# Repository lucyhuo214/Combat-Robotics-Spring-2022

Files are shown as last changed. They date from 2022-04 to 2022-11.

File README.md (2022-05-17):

# Combat-Robotics-Spring-2022
This repository includes the files for the Combat Robotics independent study at Duke University under the mentorship of Dr. Tyler Bletsch. Contributors to this project are Lucy Huo, Richard Kim, and Emily Shao.

## Project Overview
The task for this project was to build a combat robot according to the SPARC Robot Construction Specifications in the antweight class. The final project was a combat robot with a holonomic drive system. The robot uses omni wheels and an inertial measurement unit (IMU) sensor to achieve this task, correcting errors in misalignment based on IMU sensor feedback without the use of encoders on the wheels.

The primary components of the combat robot design are the three-omni-wheel kiwi drive system and the implementation of a BNO055 accelerometer to enable closed loop control, stabilizing the drive system. The software control for the robot is implemented using an Arduino Nano microcontroller.

## Holonomic Drive System
The final combat robot moves using a holonomic drive system. Holonomic drive is a drive system in which the robot’s degrees of freedom of movement are equal to the robot’s degrees of control. The combat robot in this project can move freely in the X- and Y-directions without turning, successfully implementing a holonomic drive system.

The robot uses a kiwi drive system to accomplish this, which is a form of holonomic drive that uses three omni wheels placed 120 degrees apart. Omni wheels have small rollers that are perpendicular to the direction of rotation for a wheel, allowing the wheel to roll sideways along with going forward and backwards. Omni wheels are also able to move laterally,  giving the robot full range of motion in any direction.

The CombatRoboticsHolonomic.ino script includes the robot's implementation of a holonomic drive system using kiwi drive.

## PID Closed Loop Control System
The greatest challenge that arose while implementing kiwi drive was that the robot would veer off in undesired directions due to various internal or external factors. These might include slight variations in motor performance or uneven friction within the combat arena. In most kiwi drive systems, encoders are placed on each of the three wheels to correct misalignment. However, this robot used feedback from an IMU sensor to detect and correct these misalignments without the use of any encoders.

The self-correcting control is implemented using the BNO055 accelerometer sensor. The accelerometer is mounted to the base of the robot chassis, allowing it to remain fixed to the robot and accurately gather orientation data while the robot is in motion.

The self-oriented control system is implemented using a form of closed loop control, in which portions of the output signal are used as input to the system to reduce errors or achieve system stability. For this project, the output was the yaw value from the BNO055, which was then used as an input to the kiwi drive calculations to ensure a more stable holonomic drive system.

The robot utilizes PID control, also known as Proportional, Integral, and Derivative control, to achieve this function. The proportional control adjusts the output in proportion to the error measured. The derivative control limits the overshoot of the proportional adjustment, helping the robot converge on its goal orientation faster. Finally, the integral is normally used to reduce static error in a system, but was not implemented in this project because it was negligible while in combat.

The CombatRoboticsSelfOrienting.ino script is a proof-of-concept demonstrating the ability of the robot to use PID closed loop control. The script enables the robot to always face a set absolute orientation, self correcting towards this setpoint using applications of PID control theory.

Finally, the CombatRoboticsFinalCode.ino script includes the final iteration of software control for the combat robot. It moderates the robot's holonomic drive system using PID control, while still allowing the robot driver to move and rotate in all directions in the XY-plane as desired.

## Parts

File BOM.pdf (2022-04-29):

BOM
ID
| BOM | QUANTITY
1 | 300 RPM with Metal Gearbox (N-20) | 3
2 | 2212 2200kv Brushless Motor | 1
3 | Brushed Motor ESC | 2 (or 1 if there are 3 outputs)
4 | BNO055 | 1
5 | ElectroCookie Mini Board | 1
6 | 3 pin 12V switch | 1
7 | Jst syp connector (Male + Female) | 5
8 | XT60 Connector (Male + Female) | 2
9 | Mc6c 2.4g 6ch Controller | 1

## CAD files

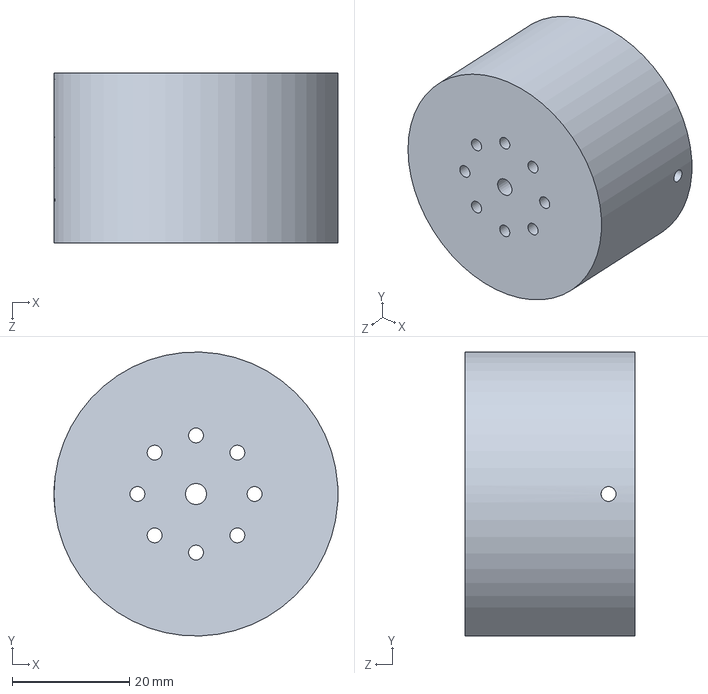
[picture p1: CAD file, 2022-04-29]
CAD Files/brushless motor insert v2.SLDPRT
48.5 x 48.5 x 29.0 mm

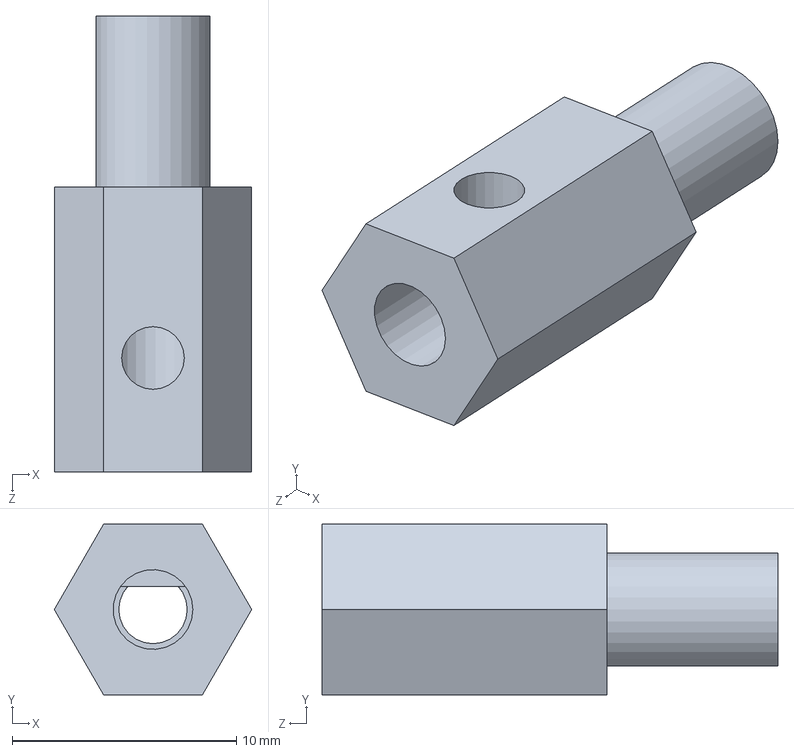
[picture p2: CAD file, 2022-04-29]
CAD Files/hex wheel insert.SLDPRT
8.80 x 7.62 x 20.3 mm

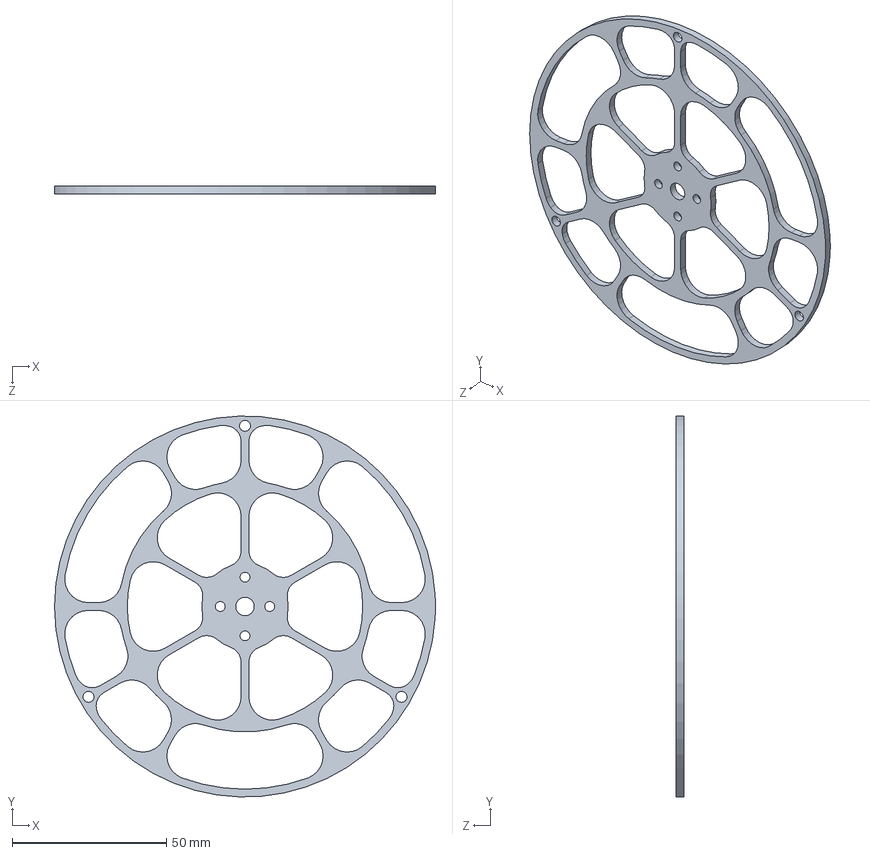
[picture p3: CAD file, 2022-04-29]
CAD Files/cover.SLDPRT
123.4 x 123.4 x 2.54 mm

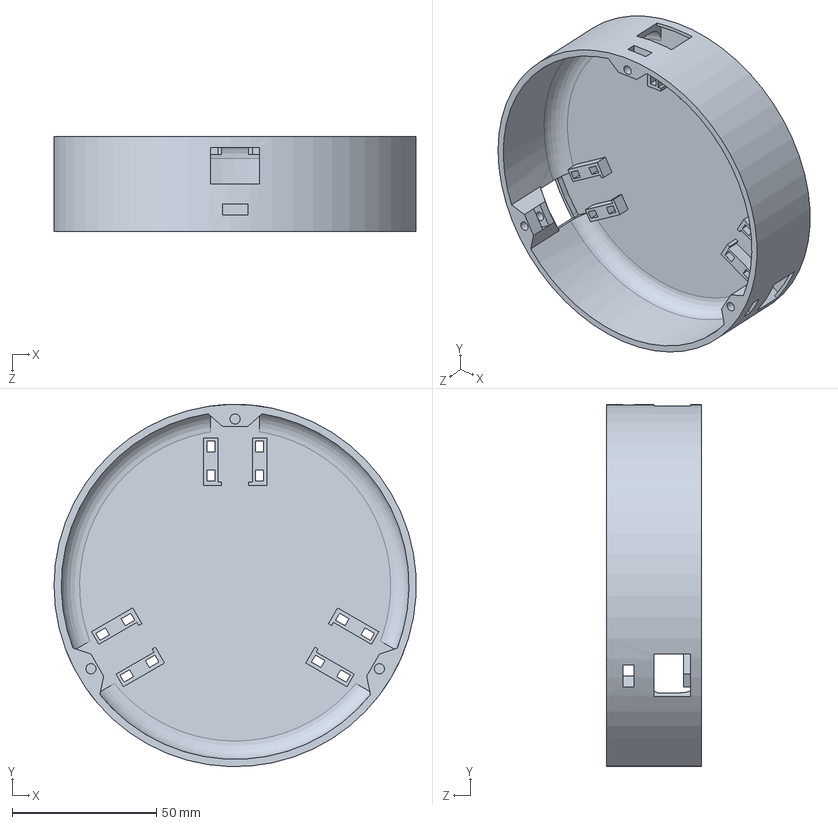
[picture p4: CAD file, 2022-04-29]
CAD Files/robot chassis.SLDPRT
125.6 x 125.7 x 33.0 mm

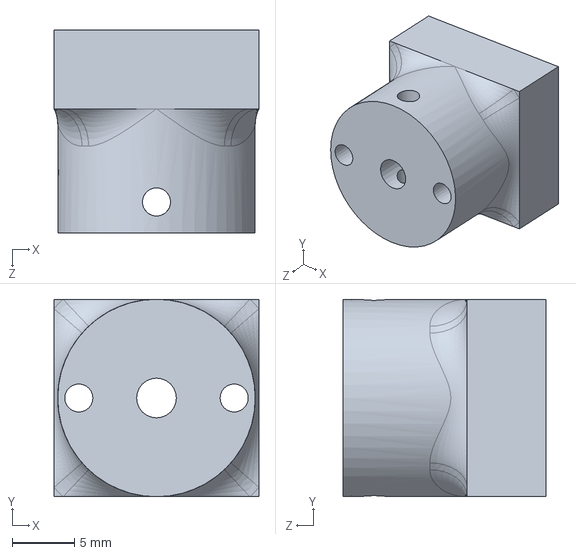
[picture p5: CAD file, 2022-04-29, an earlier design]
CAD Files/brushless motor insert v1.SLDPRT
16.5 x 15.9 x 16.4 mm

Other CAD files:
STL files/brushless motor insert v1.STL
STL files/brushless motor insert v2.STL
STL files/cover.STL
STL files/hex wheel insert.STL
STL files/robot chassis.STL

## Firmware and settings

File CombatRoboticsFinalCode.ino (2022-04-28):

/* This Arduino script includes the final integrated code for the combat robot. 
It enables a kiwi function drive system that is moderated by closed loop PID control using a BNO055 accelerometer. */

//Libraries
#include <Wire.h>
#include <Servo.h>
#include <Adafruit_Sensor.h>
#include <Adafruit_BNO055.h>
#include <utility/imumaths.h> 

//Initialize BNO sensor
#define I2C_SDA A4
#define I2C_SCL A5

Adafruit_BNO055 bno = Adafruit_BNO055(55);

//Initialize servos
Servo wheelOne;
Servo wheelTwo;
Servo wheelThree;
int thetaPin = 7;
int forwardPin = 8;
int sidePin = 9;

//Initialize kiwi drive variables
int ser1;
int ser2;
int ser3; 

//Initialize x-orientation variables
float yaw;  //Absolute x-orientation value from BNO
int error;  //Error relative to setpoint
float setpoint = 180; //Absolute orientation goal of robot

//Initialize derivative time values
float error_before;
long time_before = micros();
int error_derivative; 

//Initialize PID control constants
float p_constant = 1.5;
float d_constant = 3;

void setup() {
  Serial.begin(9600);
  Wire.begin(I2C_SDA);
  Wire.begin(I2C_SCL);
  Serial.println("Orientation Sensor Test"); Serial.println("");

  /* Initialise the sensor */
  if(!bno.begin())
  {
    /* There was a problem detecting the BNO055 ... check your connections */
    Serial.print("Ooops, no BNO055 detected ... Check your wiring or I2C ADDR!");
    while(1);
  }
  delay(1000);
  bno.setExtCrystalUse(true);

//Initialize wheels
  wheelOne.attach(2);
  wheelTwo.attach(3);
  wheelThree.attach(4);
  calib();
  delay(5000);

//Initialize remote signals
  pinMode(forwardPin, INPUT); 
  pinMode(sidePin, INPUT);
  pinMode(thetaPin, INPUT);

  Serial.println("Done with setup");
}

void loop() {
  long thetaDuration = pulseIn(thetaPin, HIGH);  //Read PWM for theta input
  float thetaVal = map((float)thetaDuration, 1750.0, 950.0, -0.5, 0.5);
   
  long fwdDuration = pulseIn(forwardPin, HIGH);  //Read PWM for fwd input
  float fwdVal = map((float)fwdDuration, 1000.0, 1980.0, -1.0, 1.0);

  long sideDuration = pulseIn(sidePin, HIGH);  //Read PWM for side input
  float sideVal = map((float)sideDuration, 2030.0, 1080.0, -1.0, 1.0);

  if(thetaDuration<1350 || thetaDuration>1550){   //If driver is manually changing theta input
    delay(100);
    sensorEvent();
    setpoint = yaw;   //Adjusts robot setpoint
  }

  //Implements goal-seeking  
  sensorEvent();  //Reads x-orientation from BNO
  adjust();   //Corrects robot orientation with proportional adjustment
  updateDer();    //Updates error_derivative value
  
  kiwiFunct(fwdVal, sideVal, thetaVal);   //Calculate servo values with kiwi drive math


  ser1+=error;  //Corrects servo values proportionally
  ser2+=error;
  ser3+=error;

  ser1+=error_derivative;   //Dampens adjustment of servo values
  ser2+=error_derivative;
  ser3+=error_derivative;
  
  wheelOne.writeMicroseconds(ser1);   //Write values to drive servos
  wheelTwo.writeMicroseconds(ser2);
  wheelThree.writeMicroseconds(ser3);
  delay(10);
}

//Cacluates error relative to robot setpoint
void calcError(){ 
  if(setpoint<=180){ //Calculates error for setpoint less than 180 degrees
    if (yaw>setpoint && yaw<setpoint+180) 
      error = rotateLeft(yaw-setpoint);
    else if(yaw>0 && yaw<setpoint)
      error = rotateRight(setpoint-yaw);
    else if(yaw>setpoint+180 && yaw<360)
      error = rotateRight(360-yaw+setpoint);
  }
  else if(setpoint>180){ //Calculates error for setpoint greater than 180 degrees
    if (yaw>setpoint-180 && yaw<setpoint) 
      error = rotateRight(setpoint-yaw);
    else if(yaw>setpoint && yaw<360)
      error = rotateLeft(yaw-setpoint);
    else if(yaw>0 && yaw<setpoint-180)
      error = rotateLeft(360-setpoint+yaw);
  }
}


//Reorients robot to face forward while driving
void adjust(){
  if(yaw!=setpoint){
    calcError();
  }
}

//Calculates derivative value in PID to dampen adjustment
void updateDer(){
  float error_now = error;   //Records current robot orientation error
  float error_delta = error_now - error_before;  //Calculates change in error

  long time_now = micros();
  long time_delta = time_now - time_before;   //Calculates change in time

  error_derivative = (int)(d_constant * error_delta / (time_delta / 100000.0));  //Calculates error derivative
  
  error_before = error_now;   //Updates current error value
  time_before = time_now;   //Updates current time value
  }

//Rotation functions with goal-seeking
int rotateRight(float angle){
  float offset = angle;
  return (int)(-1 * p_constant * offset);   //Return scaled value for rightward adjustment
}

int rotateLeft(float angle){
  float offset = angle;
  return (int)(p_constant * offset);  //Return scaled value for leftward adjustment
}

//Stops robot
void calib(){
  wheelOne.writeMicroseconds(1500);
  wheelTwo.writeMicroseconds(1500);
  wheelThree.writeMicroseconds(1500);
}

//Prints servo values
void printSer(){
  Serial.print("Ser1: " );
  Serial.print(ser1);
  Serial.print("\tSer2: " );
  Serial.print(ser2);
  Serial.print("\tSer3: " );
  Serial.println(ser3);
}

//Calculates servo values
void kiwiFunct(float fwdVal, float sideVal, float thetaVal){
  float m1 = .5 * sideVal -sqrt(3)/2 * fwdVal + thetaVal;
  float m2 = .5 * sideVal + sqrt(3)/2 * fwdVal + thetaVal;
  float m3 = -1 * sideVal + thetaVal;

  float avg1 = (m1)/3.0;
  float avg2 = (m2)/3.0;
  float avg3 = (m3)/3.0;
  
  ser1 = (int)(map(avg1, -1, 1, 1000, 2000));
  ser2 = (int)(map(avg2, -1, 1, 1000, 2000));
  ser3 = (int)(map(avg3, -1, 1, 1000, 2000));
}

/* Get a new sensor event */ 
void sensorEvent(){
  sensors_event_t event;   //Reads absolute x-orientation from BNO
  bno.getEvent(&event);
  yaw = event.orientation.x;   //Updates yaw value
}

/* Display sensor floating point data */
void printYaw(){
  Serial.print("\tyaw:" );
  Serial.println(yaw, 4);
}

//Takes value v in range [a,b] and maps to corresponding value in range [c,d]
float map(float v, float a, float b, float c, float d){
  return (v-a) * (d-c) / (b-a) + c;
}

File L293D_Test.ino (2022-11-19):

//L293D
//Motor A
const int motorPin1  = 5;  // Pin 14 of L293
const int motorPin2  = 6;  // Pin 10 of L293
//Motor B
const int motorPin3  = 2; // Pin  7 of L293
const int motorPin4  = 3;  // Pin  2 of L293
//note that right now pin 2 is digital, rest can are analog

//This will run only one time.
void setup(){
 
    //Set pins as outputs
    pinMode(motorPin1, OUTPUT);
    pinMode(motorPin2, OUTPUT);
    pinMode(motorPin3, OUTPUT);
    pinMode(motorPin4, OUTPUT);
    
    //Motor Control - Motor A: motorPin1,motorpin2 & Motor B: motorpin3,motorpin4

    
}


void loop(){
   //digital motor output
 /* //This code  will turn Motor A clockwise for 2 sec.
    digitalWrite(motorPin1, HIGH);
    digitalWrite(motorPin2, LOW);
//    digitalWrite(motorPin3, LOW);
//    digitalWrite(motorPin4, LOW);
    delay(2000); 
    
    //This code will turn Motor A counter-clockwise for 2 sec.
    digitalWrite(motorPin1, LOW);
    digitalWrite(motorPin2, HIGH);
//    digitalWrite(motorPin3, LOW);
//    digitalWrite(motorPin4, LOW);
    delay(2000);


    //This code  will turn Motor B clockwise for 2 sec.
//    digitalWrite(motorPin1, LOW);
//    digitalWrite(motorPin2, LOW);
    digitalWrite(motorPin3, HIGH);
    digitalWrite(motorPin4, LOW);
    delay(2000); 
    
    //This code will turn Motor B counter-clockwise for 2 sec.
//    digitalWrite(motorPin1, LOW);
//    digitalWrite(motorPin2, LOW);
    digitalWrite(motorPin3, LOW);
    digitalWrite(motorPin4, HIGH);
    delay(2000);    
*/
  for (int i = 0; i<250; i+=10){
    analogWrite(motorPin1, i);
    analogWrite(motorPin4, 255-i);
    delay(500);
  }

    
    
    //And this code will stop motors
    digitalWrite(motorPin1, LOW);
    digitalWrite(motorPin2, LOW);
    digitalWrite(motorPin3, LOW);
    digitalWrite(motorPin4, LOW);
    delay(2000);
}

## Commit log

2022-04-28 Rename CoRoManualRot.ino to CombatRoboticsFinal.ino
    This Arduino script includes the final integrated code for the combat robot. It enables a kiwi function drive system that is moderated by closed loop PID control using a BNO055 accelerometer.
2022-04-28 Updated
    This Arduino script enables kiwi drive functionality in the combat robot moderated by closed loop PID control using a BNO055 accelerometer. It enables the robot to always orient itself to some absolu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
2022-04-28 Updated
    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
2022-04-28 Rename CombatRoboticsSelfOrientation.ino to CombatRoboticsSelfOrient.ino
    This Arduino script enables a kiwi function drive system that is moderated by closed loop control using a BNO055 accelerometer. It enables the robot to always reorient itself to a set absolute orient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
2022-04-28 Updated
    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
2022-04-28 Update CombatRoboticsFinalCode.ino
    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
2022-04-28 Update CombatRoboticsSelfOrienting.ino
    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
2022-04-29 Update and rename CoRoCJMCU.ino to CombatRoboticsHolonomic.ino
    This Arduino script implements a holonomic drive system using kiwi drive. This was an early version of the drive system code without IMU feedback.
